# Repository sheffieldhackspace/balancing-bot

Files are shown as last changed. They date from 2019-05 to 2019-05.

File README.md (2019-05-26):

The **inkscapeFiles** directory contains all the files and instructions needed to laser cut a frame for the self-balancing bot.

All the files needed for the pcb (including gerber files) are located in **kicadFiles**.

Remember to solder the HC-05 bluetooth module on last!
The R1 resistor value should be 2K ohms, whilst for R2 it's 1k ohms.

The Arduino code is a modified version of that developed by [http://www.klikrobotics.com](http://www.klikrobotics.com) and was downloaded from their repository at [https://github.com/garethnisbet/T-BOTS](https://github.com/garethnisbet/T-BOTS). The code was branched off in Oct 2018 and is therefore out of date but it works!

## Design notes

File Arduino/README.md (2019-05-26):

To get the self-balancing bot up and running you'll first need to copy the contents of **libraries** to your **Arduino/libraries** folder on your system.

#

If you're using a 3xAA battery pack then make sure to comment out 

```
#define USE_LITHIUM_BATT
```

in the code and set the VSel jumpers to 5V. Otherwise set them to 7.4V.

#

Upload **ember/ember.ino** to the Nano. Open up the arduino serial monitor and set the baud rate to 38400. With the motors and batteries disconnected, insert the usb cable and hold the pcb upright and you should see the pitch values being output to the serial monitor.

You can then comment out 

```
Serial.println(CFilteredlAngleY)
```

once this test is completed.  

#

Now go to **changebaudrate** and follow the instructions there.

Install the Joystick BT Commander app on your phone and follow the instructions at

[http://www.klikrobotics.com/Controllers2.html](http://www.klikrobotics.com/Controllers2.html)

to configure it. For the labels, use P instead of KPS, and I instead of KP. If you switch on the bot and connect to it via bluetooth then you should see some values for P, I and Trim appear in the app.  

#

The next step is to follow the instructions in the **deadbands** directory first and then in **ember** to get the robot up and running!

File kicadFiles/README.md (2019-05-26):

Drag and drop the /gerber files to 

[https://www.pcbgogo.com/GerberViewer.html](https://www.pcbgogo.com/GerberViewer.html)

to view the pcb in 2D, or to

[http://mayhewlabs.com/webGerber](http://mayhewlabs.com/webGerber)

to view them in 3D.

If you want to order some pcbs from somewhere then usually you need to .zip these files and then upload them.  
#

The pcb designs were created using KiCad v5.0. If you want to modify the design and create your own gerber files then you need to do the following:

1. Open pcb01.kicad_pcb with pcbnew
2. Go to File -> File Plot
3. Press the 'Plot' button and then press the 'Generate Drill Files' button
4. Select 'Zeros Format:Keep zeros' and then press the 'Generate Drill File' button.

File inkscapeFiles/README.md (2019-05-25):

# balancing-bot

For the inkscape files the laser cutting should be done in the following order: 

1. Red
2. Green
3. Black

Don't cut the blue lines because these are only used as guidelines for the frame design!

May 2019

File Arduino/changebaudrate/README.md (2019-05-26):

First upload **changebaudrate.ino** and then remove the usb cable and make sure the power is turned off on the robot.

Hold down the little button on the HC-05 bluetooth module and plug the cable back in again. Wait a few seconds until the LED starts flashing slowly and release.

Open up the serial monitor and select **Autoscroll**, **Both NL & CR** and **9600**. You should see some instructions appear in the monitor. Type

**AT+UART=38400,0,0**

into the serial monitor and hit enter. It should respond with "OK".

The baud rate on the HC-05 should be set to the right value now!

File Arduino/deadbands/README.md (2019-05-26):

You'll first need to upload **deadbands.ino** to the Nano.

Optimize the parameters **m1ndb**, **m1pdb**, **m2ndb**, **m2pdb** (as instructed in the code) so that the motors barely run in both directions. Lay the robot flat to find the values for the motors going in one direction, and then flip it over to get the values going in the opposite direction.

If you're using 3xAA batteries then subtract 2 from these values and put them into **ember/ember.ino**, and if you're using Li-ion batteries then subtract 10 from them.

You may need to tinker with these paramaters a bit to get the optimum values for smooth balancing. If there's a slight rotational drift then try adding 1 to both **m1ndb** and **m1pdb** or something similar.

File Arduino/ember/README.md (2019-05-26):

This is where the main code for the self-balancing bot is located. The file **ember.ino** is the one you want to upload.

If the bot rushes forwards or backwards then you can alter the **Trim** value using the joystick BT commander app to get it to stand still. You can change the value of **gtrim** in the code so that you don't always have to do this.

The balancing is controlled by a PID loop. The 'Proportional' parameter is given by the values **gyroKp** and **KP** (which should be set the same), whereas the 'Integral' value is given by **gyroKi** and **KI** (also should be the same). You can tune these values using the BT commander app and, as before, the values can be hardcoded so they don't have to be setup again.

If you want to print anything out to the serial monitor then make sure you use something like

```
#ifndef USE_HARDWARE_SERIAL
	Serial.println(CFilteredlAngleY);
#endif
```

which ensures that there's no interference with data being sent to the HC-05 when using hardware serial instead of software serial.

And if you do want to use hardware serial to communicate with the HC-05 bluetooth module, uncomment out 

```
//#define USE_HARDWARE_SERIAL
```
before uploading, and then switch the SerialSel jumpers to the HW setting. You'll need to remove the jumpers every time you want to upload code again.

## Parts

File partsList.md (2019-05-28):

Arduino nano

TB6612FNG motor driver

MPU6050 accelerometer/gyro

HC-05 bluetooth module

PCB (see kicadFiles directory)

Sheet of 3mm thick acrylic for frame (at least 16x9cm big)

2x wheels (approx 40mm, 3mm d-shaft type)

2x n20/6v/300rpm dc motors

3xAA batteries (or 2x18650 Li-ion batteries)

3xAA battery holder (or 2x18650 Li-ion battery holder)

3x double terminal blocks (0.1" pitch)

1 DPDT switch (0.1" pitch)

3x jumpers (0.1" pitch)

Strip of 9x1 0.1" pitch headers (or a 3x1 header plus a 3x2 header)

2200uF/16v capacitor (47uF is ok if using Li-ion battery)

One 1K ohm and one 2K ohm resistor

Screws: 6x m2x20mm, 4x m2x8mm, 2x counter-sunk m3x8mm 

Nuts: 10x m2, 2x m3 (both preferably nylon)

Optional: piece of elastic band + double sided tape (to dampen motors and increase stability)

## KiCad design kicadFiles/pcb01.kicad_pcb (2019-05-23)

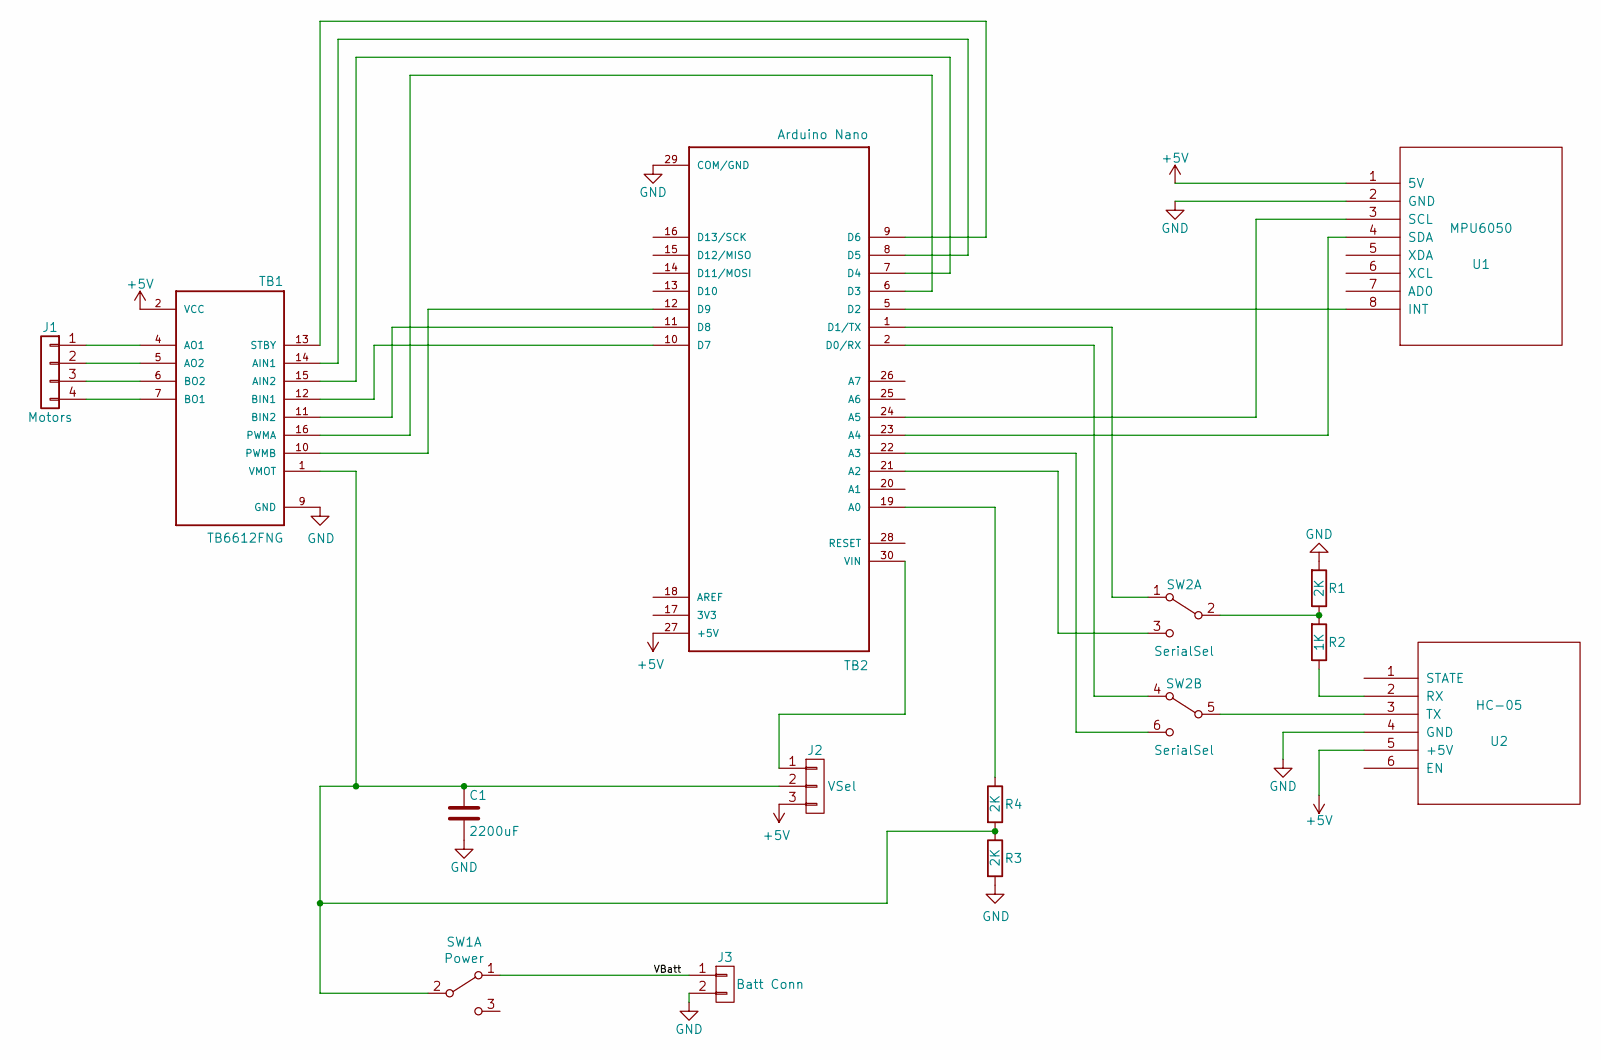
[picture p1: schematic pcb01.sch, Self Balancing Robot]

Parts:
C1: 2200uF; C_Radial_D10.0mm_H20.0mm_P5.00mm
J1: Motors; PinHeader_1x04_P2.54mm_Vertical
J2: VSel; PinHeader_1x03_P2.54mm_Vertical
J3: Batt Conn; PinHeader_1x02_P2.54mm_Vertical
R1, R3, R4: 2K; R_Axial_DIN0207_L6.3mm_D2.5mm_P10.16mm_Horizontal
R2: 1K; R_Axial_DIN0207_L6.3mm_D2.5mm_P10.16mm_Horizontal
SW1: Power; SW_CuK_JS202011CQN_DPDT_Straight
SW2: SerialSel; SW_CuK_JS202011CQN_DPDT_Straight
TB1: TB6612FNG; Pololu_Breakout-16_15.2x20.3mm
TB2: Arduino Nano; Arduino_Nano
U1: MPU6050; PinHeader_1x08_P2.54mm_Vertical
U2: HC-05; PinHeader_1x06_P2.54mm_Vertical

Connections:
+5V: J2.3, TB1.2 (VCC), TB2.27 (+5V), U1.1 (5V), U2.5 (+5V)
/VBatt: J3.1, SW1.1 (A)
COM/GND: C1.2, J3.2, R1.2, R3.2, TB1.3 (GND), TB1.8 (GND), TB1.9 (GND), TB2.4 (COM/GND), TB2.29 (COM/GND), U1.2 (GND), U2.4 (GND)
unnamed: C1.1, J2.2, R3.1, R4.2, SW1.2 (B), TB1.1 (VMOT)
unnamed: J1.1, TB1.4 (AO1)
unnamed: J1.2, TB1.5 (AO2)
unnamed: J1.3, TB1.6 (BO2)
unnamed: J1.4, TB1.7 (BO1)
unnamed: J2.1, TB2.30 (VIN)
unnamed: R1.1, R2.2, SW2.2 (B)
unnamed: R2.1, U2.2 (RX)
unnamed: R4.1, TB2.19 (A0)
unnamed: SW2.1 (A), TB2.1 (D1/TX)
unnamed: SW2.3 (C), TB2.21 (A2)
unnamed: SW2.4 (A), TB2.2 (D0/RX)
unnamed: SW2.5 (B), U2.3 (TX)
unnamed: SW2.6 (C), TB2.22 (A3)
unnamed: TB1.10 (PWMB), TB2.12 (D9)
unnamed: TB1.11 (BIN2), TB2.11 (D8)
unnamed: TB1.12 (BIN1), TB2.10 (D7)
unnamed: TB1.13 (STBY), TB2.9 (D6)
unnamed: TB1.14 (AIN1), TB2.8 (D5)
unnamed: TB1.15 (AIN2), TB2.7 (D4)
unnamed: TB1.16 (PWMA), TB2.6 (D3)
unnamed: TB2.5 (D2), U1.8 (INT)
unnamed: TB2.23 (A4), U1.4 (SDA)
unnamed: TB2.24 (A5), U1.3 (SCL)

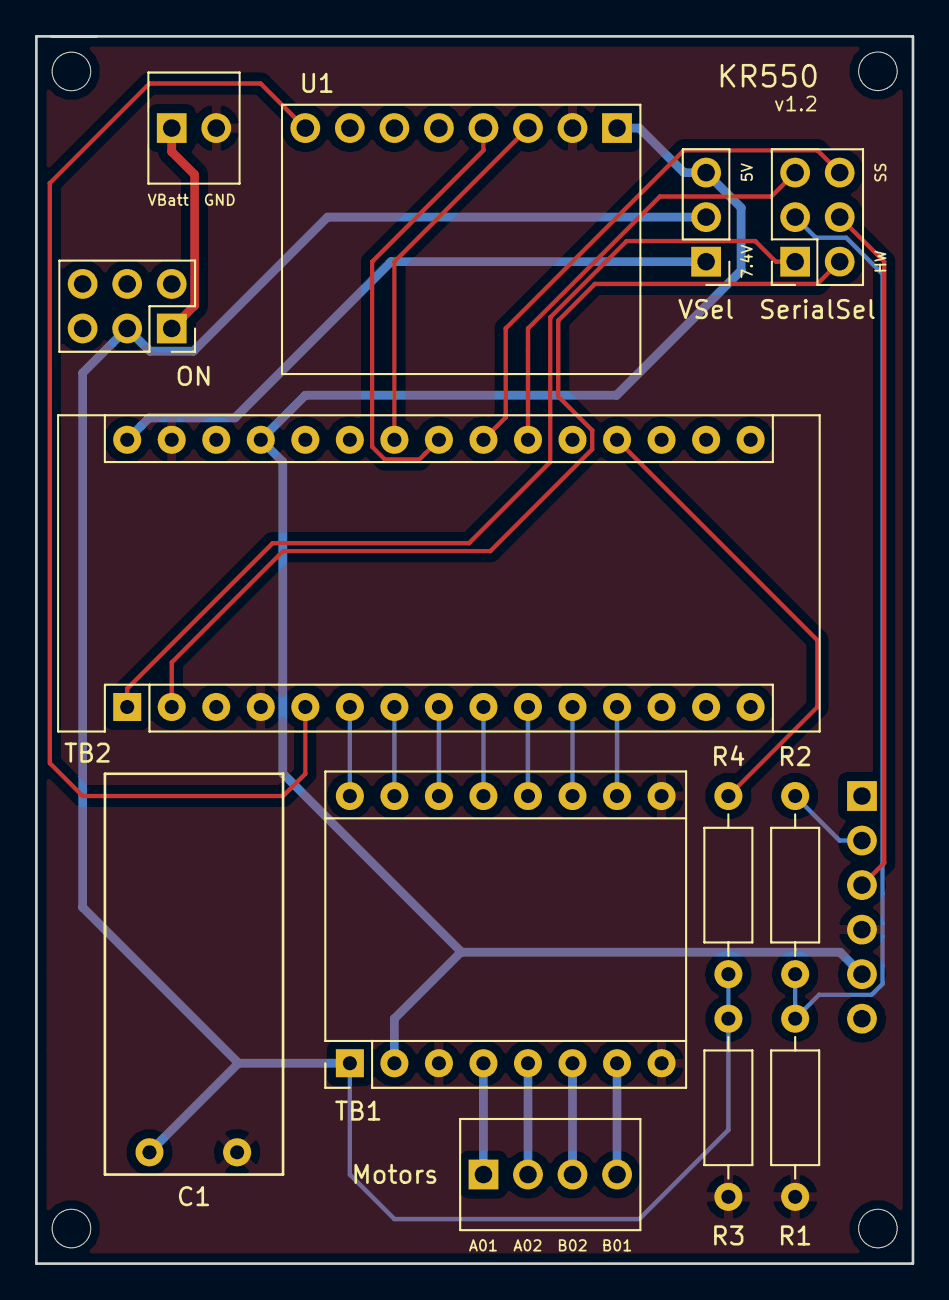
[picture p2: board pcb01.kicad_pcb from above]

Board: 2 copper layers, 50.0 x 70.0 mm, 14 parts (1 on the bottom side), 27 nets.

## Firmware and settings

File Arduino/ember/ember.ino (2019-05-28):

/**********************************************************************
 * 
 *    Ember (self-balancing robot)
 *    v1.2
 * 
 *    May 2019
 * 
 * 
 * 
 *    (set SerialSel jumpers to "SS" before uploading this code)
 * 
 *  
 *  
 **********************************************************************/

/*
This code is a modified version of that developed by klikrobotics and was downloaded from their repository at 
https://github.com/garethnisbet/T-BOTS
The code here was branched off in Oct 2018 and is therefore out of date but it works!
*/

#include <TaskScheduler.h>
#include <Motor.h>
#include <PID_v1.h>
#include <Filters.h>
#include <SoftwareSerial.h>
#include <Wire.h>
#include "Combination_Filter.h"

//#define USE_HARDWARE_SERIAL
#define USE_LITHIUM_BATT

///////////////////////////// Setup Bluetooth Control   ///////////////////////////

#define    STX          0x02
#define    ETX          0x03

int joyX, joyY, joyXbefore, joyYbefore, joyXdiff, joyYdiff;
float joyXf, joyYf;
float backoff;

//controller_sensitivity determines the maximum speed of the bot
#ifdef USE_LITHIUM_BATT
float controller_sensitivity = 2.0;
#else
float controller_sensitivity = 1.5;
#endif

#ifdef USE_HARDWARE_SERIAL
auto& BTSerial = Serial;
#else
SoftwareSerial BTSerial(17, 16);                          // (RX,TX)
#endif

byte cmd[8] = {0, 0, 0, 0, 0, 0, 0, 0};                   // bytes received
byte buttonStatus = 0;                                    // first Byte sent to Android device
String displayStatus = "----";

/////////////////////////////////////////////////////////////////////////////////

bool startFlag = false;

int kp, ki, kd; // for inread function
int gyrocounter, commandcounter;

float gyrocomp;
float forward, remoteclock, ac2, accXF;
float spinval;
float spinfactor = 0.8;
float filterFrequency = 1;
float g = 9.81, pi = 3.1416, h = 0.08;
float dh, th, phi, v, vxy, vx, vy, vz, norm, vxs, vys, angout;
float accX, accY, accZ;



////////////////////  Speed and Stability tunings   /////////////////////////


float filter_weighting = 0.003; // may need to increase this to 0.005 or 0.006 if motors aren't damped
//float filter_weighting = 0.015; // original value used in kilkrobotics T-bot code

float speedpidsampletime = 2;
float gyropidsampletime = 2;

#ifdef USE_LITHIUM_BATT

float gtrim = -3.15;   // compensation for drift in forward or reverse direction.
float rtrim = 0.0; // compensation for rotational drift.
double speedKp=0.08, speedKi=0, speedKd=0.0, KPS = 0.08, KP = 3.0, KI = 70, KPS_last, KP_last, KI_last; 
double gyroKp=3.0, gyroKi=70, gyroKd=0.0;  //Ki = 90 good too

#else

double speedKp=0.08, speedKi=0, speedKd=0.0, KPS = 0.08, KP = 6.0, KI = 120, KPS_last, KP_last, KI_last; 
double gyroKp=6.0, gyroKi=120, gyroKd=0.0;  
float gtrim = 5.5;   // compensation for drift in forward or reverse direction.
float rtrim = 0.0; // compensation for rotational drift.

#endif
double speedSetpoint, speedInput, speedOutput;
PID speedPID(&speedInput, &speedOutput, &speedSetpoint, speedKp, speedKi, speedKd, DIRECT);

double gyroySetpoint, gyroyInput, gyroyOutput;
PID gyroyPID(&gyroyInput, &gyroyOutput, &gyroySetpoint, gyroKp, gyroKi, gyroKd, DIRECT);



/////////////////////          Setup Motors             /////////////////////////


#ifdef USE_LITHIUM_BATT //deadbands change when using different batteries



const int m1ndb = 4, m1pdb = 5, m2ndb = 7, m2pdb = 8; /*
    The values the deadband code gave were: 14,15,18,19 
    These needed to be reduced by approx 10 and then adjusted to get smooth balancing (and reduce rotational drift)
    Default values: const int m1ndb = 6, m1pdb = 6, m2ndb = 6, m2pdb = 6; */


#else


const int m1ndb = 16, m1pdb = 16, m2ndb = 19, m2pdb = 19; /*
    The values the deadband code gave were: 18,18,21,21
    These needed to be reduced by approx 2 and then adjusted to get smooth balancing (and reduce rotational drift)
    Note that 3xAA batteries gives 4.5V, whilst usb gives 5V, so do final test with usb cable unplugged 
    Default values: const int m1ndb = 16, m1pdb = 16, m2ndb = 16, m2pdb = 16; */

#endif




const int m2stby = 6, m2ain1 = 4, m2ain2 = 5, m2pwmpin = 3,  mpsfactor = 257;
Motor m1 = Motor(m2ain1, m2ain2, m2stby, m2pwmpin, m1ndb, m1pdb, mpsfactor);

const int m1stby = 6, m1ain1 = 8, m1ain2 = 7,  m1pwmpin = 9;
Motor m2 = Motor(m1ain1, m1ain2, m1stby, m1pwmpin, m2ndb, m2pdb, mpsfactor);

float lambdaM1n=(255-m1ndb)/321.0, lambdaM2n=(255-m2ndb)/321.0, lambdaM1p=(255-m1pdb)/321.0, lambdaM2p=(255-m2pdb)/321.0;



///////////////////   Setup Gyro with Combination Filter   /////////////////////

CFilter CFilterY; // Create the CFilter instances

double gyroX, gyroY, gyroZ;
int16_t tempRaw;
double  gyroYangle; // Angle calculate using the gyro only
double CFilteredlAngleY; // Calculated angle using a CFilter
double pitch, roll, gyroYrate, gyroangle;
uint32_t timer;
uint8_t i2cData[14]; // Buffer for I2C data
double gyroxoffset, gyroyoffset;



///////////////////         Setup Scheduled Tasks         /////////////////////


void CFilterReadCallBack();             // Filtered Angle Readback
void speedPIDCallBack();                // Speed PID Control Loop
void gyroPIDCallBack();                 // Stability PID Control Loop
void bluetoothCallBack();               // Bluetooth IO Read Loop



///////////////////    Set Number of Loops and Frequency  /////////////////////


Task tCFilterRead(2, TASK_FOREVER, &CFilterReadCallBack);
Task tGyroPID(4, TASK_FOREVER, &gyroPIDCallBack);
Task tspeedPID(4, TASK_FOREVER, &speedPIDCallBack);

#ifdef USE_HARDWARE_SERIAL
Task bluetooth(8, TASK_FOREVER, &bluetoothCallBack);  
#else
Task bluetooth(20, TASK_FOREVER, &bluetoothCallBack); 
#endif

Scheduler runner;

void bluetoothCallBack() {
  if (BTSerial.available())  {                          // data received from smartphone
    //delay(2);
    cmd[0] =  BTSerial.read();
    if (cmd[0] == STX)  {
      int i = 1;
      while (BTSerial.available())  {
        // delay(1);
        cmd[i] = BTSerial.read();
        if (cmd[i] > 127 || i > 7)                 break; // Communication errordelay
        if ((cmd[i] == ETX) && (i == 2 || i == 7))   break; // Button or Joystick data
        i++;
      }
      if     (i == 2)          getButtonState(cmd[1]);  // 3 Bytes  ex: < STX "C" ETX >
      if (i == 7)          getJoystickState(cmd);  // 6 Bytes  ex: < STX "200" "180" ETX >
    }
  }
  if (KPS + KP + KI !=  KPS_last + KP_last + KI_last) {
    speedPID.SetTunings(KPS, speedKi, speedKd);
    gyroyPID.SetTunings(KP, KI, gyroKd);
  }
  KPS_last = speedPID.GetKp();
  KP_last = gyroyPID.GetKp();
  KI_last = gyroyPID.GetKi();

  
  BTSerial.print((char)STX);
  BTSerial.print((char)0x1);
  BTSerial.print(KP_last);
  BTSerial.print((char)0x4);
  BTSerial.print(KI_last);
  BTSerial.print((char)0x5);
  //BTSerial.print(KI_last);
  BTSerial.print(gtrim);
  BTSerial.print((char)ETX);
  
}
void CFilterReadCallBack() {
  gyroread();

}

void speedPIDCallBack() {
  if (abs(joyXf) > 60) { // Compensation to prevent robot falling over when spinning

    speedSetpoint = controller_sensitivity * ((abs(joyYf) + 90 + backoff) / mpsfactor);
  }
  else {
    speedSetpoint = controller_sensitivity * ((joyYf + backoff) / mpsfactor);
  }
  if (vxy != vxy) {
    speedInput = 0;
  }
  else {
    speedInput = -vxy;
  }
  speedPID.Compute();
  v2ang(h, speedOutput);
  gyroySetpoint = angout;

}


void gyroPIDCallBack() {

  gyroyInput = CFilteredlAngleY - gtrim; 
  gyroyPID.Compute();

  spinval = -spinfactor * joyXf / mpsfactor;
  vel(h, gyroyOutput); // calculates vxy

  if(!startFlag)  // motors run from 100ms until 850ms after boot for some reason (prob a Scheduler/Task issue) 
  {
    if(millis() > 850) 
      startFlag = true;
  }

  // stop the motors if pitch >40 degrees
  if (abs(CFilteredlAngleY) > 40 || !startFlag) { 

    analogWrite(m1pwmpin, 0); 
    analogWrite(m2pwmpin, 0);
 
    
  }
  else {

#ifndef USE_HARDWARE_SERIAL 
    Serial.println(CFilteredlAngleY);
#endif

    if((vxy-spinval+rtrim)<0)
    {      
      m1.speed((vxy-spinval+rtrim)*lambdaM1n);
      m2.speed((vxy+spinval-rtrim)*lambdaM2n);

    }
    else
    {      
      m1.speed((vxy-spinval+rtrim)*lambdaM1p);
      m2.speed((vxy+spinval-rtrim)*lambdaM2p);

    }
  }
}

void setup () {
  Wire.begin();

  ////// Scale up PWM frequency to avoid annoying high pitch motor noise ///////

  int Eraser = 7; // this is 111 in binary and is used as an eraser  TCCRnB where n
  int Prescaler = 1;// this could be a number in [1 , 6]. In this case, 3 corresponds in binary to 011.
  TCCR1B &= ~Eraser; // this operation (AND plus NOT),  set the three bits in TCCR3B to 0
  TCCR1B |= Prescaler;//this operation (OR), replaces the last three bits in TCCR2B with our new value 011


  /////////////////////     Setup i2c commuication for Gyro       //////////////

  TWBR = ((F_CPU / 400000L) - 16) / 2; // Set I2C frequency to 400kHz
  i2cData[0] = 7; // Set the sample rate to 1000Hz - 8kHz/(7+1) = 1000Hz
  i2cData[1] = 0x00; // Disable FSYNC and set 260 Hz Acc filtering, 256 Hz Gyro filtering, 8 KHz sampling
  i2cData[2] = 0x00; // Set Gyro Full Scale Range to ±250deg/s
  i2cData[3] = 0x00; // Set Accelerometer Full Scale Range to ±2g
  while (i2cWrite(0x19, i2cData, 4, false)); // Write to all four registers at once
  while (i2cWrite(0x6B, 0x01, true)); // PLL with X axis gyroscope reference and disable sleep mode
  while (i2cRead(0x75, i2cData, 1));
  if (i2cData[0] != 0x68) { // Read "WHO_AM_I" register
    //Serial.print(F("Error reading sensor"));
    while (1);
  }
  delay(100); // Wait for sensor to stabilize


  ////////////////           Set PID output limits       /////////////////////

  speedPID.SetOutputLimits(-0.2, 0.2); 
  speedPID.SetMode(AUTOMATIC);
  speedPID.SetSampleTime(speedpidsampletime);

  gyroyPID.SetOutputLimits(-90, 90);
  gyroyPID.SetMode(AUTOMATIC);
  gyroyPID.SetSampleTime(gyropidsampletime);

  ///////////   Setup Serial and Bluetooth communication   ////////////////////

  // pinMode(15, OUTPUT);  // this pin will pull the HC-05 pin 34 (key pin) HIGH to switch module to AT mode
  // digitalWrite(15, LOW); //Some modules reqire this to be set to HIGH
  // Others require these lines to be commented out.

#ifndef USE_HARDWARE_SERIAL
  Serial.begin(38400);
#endif
  BTSerial.begin(38400);
  
  while (BTSerial.available())  BTSerial.read();



  /////////////////         Start Scheduled Tasks         /////////////////////


  runner.init();


  runner.addTask(tCFilterRead);
  runner.addTask(tspeedPID); // Add Speed PID control
  runner.addTask(tGyroPID);  // Add Stability PID control
  runner.addTask(bluetooth); // Add Bluetooth Comunication

  tGyroPID.enable();
  tspeedPID.enable();
  bluetooth.enable();
  tCFilterRead.enable();

  
}

void loop () {
  
  runner.execute();

}

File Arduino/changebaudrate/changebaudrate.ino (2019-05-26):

#include <SoftwareSerial.h>

SoftwareSerial BTSerial(17, 16); // RX | TX


void setup()
{
 // pinMode(15, OUTPUT);  // this pin will pull the HC-05 pin 34 (key pin) HIGH to switch module to AT mode
 // digitalWrite(15, HIGH); //some modules require these lines to be commented out
  Serial.begin(9600);
  Serial.println("Commands for HC-05");
  Serial.println(" ");
  Serial.println("Type AT+NAME:NewName to change your T-BOTS name.");
  Serial.println("Type AT+UART=38400,0,0 to change baud rate");
  Serial.println("Type AT+ADDR? to get the mac address (YOU WILL NEED THIS LATER)");
  Serial.println(" ");

  Serial.println("Enter AT commands:");
  
  // HC-05 default BAUD rate is 38400 for AT command mode
  // AT-09 default BAUD rate is 9600. There is no default AT mode BAUD rate
  // so BTSerial.begin(38400) will have to be changed to BTSerial.begin(57600)
  // and uploaded again to the T-Bot if you want to continue in AT mode after 
  // issuing AT+BAUD7

  BTSerial.begin(38400);  // HC-05 default speed in AT command more

}

void loop()
{
  // Keep reading from HC-05 and send to Arduino Serial Monitor
  if (BTSerial.available())
    Serial.write(BTSerial.read());

  // Keep reading from Arduino Serial Monitor and send to HC-05
  if (Serial.available())
    BTSerial.write(Serial.read());
}
